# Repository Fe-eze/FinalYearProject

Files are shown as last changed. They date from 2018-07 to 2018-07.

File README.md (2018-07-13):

# FinalYearProject
My final year project. Formula Student: Design of a Battery and Battery Management System

I started by designing the battery from a 20700 (as you see in design 1 & 2 in the deliverables) but had to do a hard pivot when I noticed the design didn't seem to be feasible. The final design was done with 18650 cells.

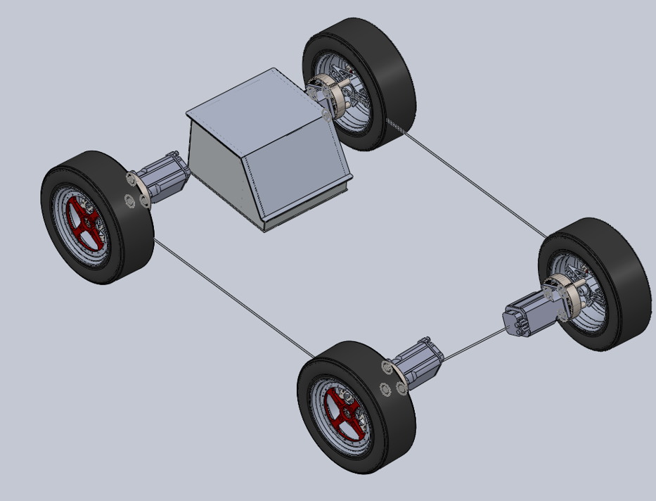
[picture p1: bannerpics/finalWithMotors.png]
Battery Pack with Motors

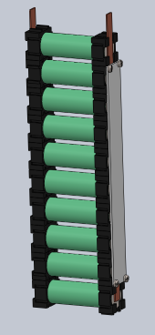
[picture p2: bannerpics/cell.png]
Cells Joined in a string

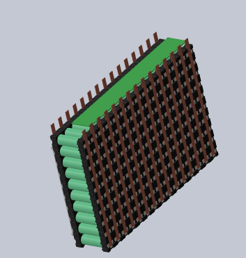
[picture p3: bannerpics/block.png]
Battery Strings joined to form a block

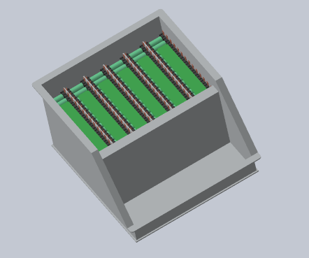
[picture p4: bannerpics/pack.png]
Final Battery Pack

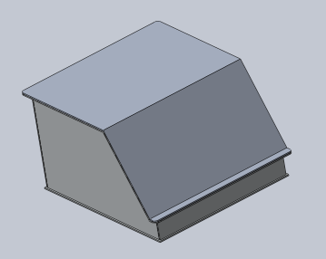
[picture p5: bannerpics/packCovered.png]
Battery Pack with Cover


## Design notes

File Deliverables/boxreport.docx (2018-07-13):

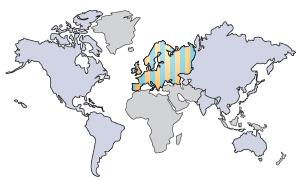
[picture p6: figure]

| Manufacturing Region The choice of manufacturing region determines the energy sources and technologies used in the modeled material creation and manufacturing steps of the product’s life cycle.
| Use Region The use region is used to determine the energy sources consumed during the product’s use phase (if applicable) and the destination for the product at its end-of-life. Together with the manufacturing region, the use region is also used to estimate the environmental impacts associated with transporting the product from its manufacturing location to its use location.

Summary

Learn more about Life Cycle Assessment (http://www.solidworks.com/sustainabilityinfo)

Sustainability Report
Model Name: | | | | | | | | Weight: | | 15856.92 g
| | | | | | | | Built to last: | | 0.417 year
| | | | | | | | Duration of use: | | 5.0 year
Assembly Process Region: Europe Energy type: Electricity Energy amount: 0.00 kWh Built to last: 0.417 year | | | | | | Use Region: Europe Energy type: None Energy amount: 0.00 kWh Duration of use: 5.0 year
Transportation Truck distance: 1900 km Train distance: 0.00 km Ship distance: 0.00 km Airplane Distance: 0.00 km | | | | | | End of Life Recycled: 25 % Incinerated: 24 % Landfill: 51 %

Comments
Click here for alternative units such as ‘Miles Driven in a Car’ (http://www.solidworks.com/plugins/sustainability/calculator.htm?LANG=en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)

Sustainability Report
Model Name: | | | | | | | Weight: | | 15856.92 g
| | | | | | | Built to last: | | 0.417 year
| | | | | | | Duration of use: | | 5.0 year

Environmental Impact (calculated using TRACI impact assessment methodology)
Carbon Footprint Material: 990 kg CO2e Manufacturing: 45 kg CO2e Use: 0.00 kg CO2e Transportation: 23 kg CO2e End of Life: 130 kg CO2e 1200 kg CO2e | | | | | | Total Energy Consumed Material: 1.2E+4 MJ Manufacturing: 750 MJ Use: 0.00 MJ Transportation: 350 MJ End of Life: 95 MJ 1.3E+4 MJ
Air Acidification Material: 320 mol H⁺ e Manufacturing: 15 mol H⁺ e Use: 0.00 mol H⁺ e Transportation: 9.4 mol H⁺ e End of Life: 5.1 mol H⁺ e 350 mol H⁺ e | | | | | | Water Eutrophication Material: 0.086 kg N e Manufacturing: 5.4E-3 kg N e Use: 0.00 kg N e Transportation: 9.0E-3 kg N e End of Life: 0.033 kg N e 0.133 kg N e

Material Financial Impact | 176.10 USD

Comments
Click here for alternative units such as ‘Miles Driven in a Car’ (http://www.solidworks.com/plugins/sustainability/calculator.htm?LANG=en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)

Sustainability Report
Model Name: | | | | | Weight: | 15856.92 g
| | | | | Built to last: | 0.417 year
| | | | | Duration of use: | 5.0 year

Component Environmental Impact

Top Ten Components Contributing Most to the Four Areas of Environmental Impact

Component | Carbon | | | | | | | | | | Water | | | | | | | | | | Air | | | | | | | | | Energy
box_TopCover | 37 | | | | | | | | | | 3.3E-3 | | | | | | | | | | 11 | | | | | | | | | 460
box_base | 33 | | | | | | | | | | 2.9E-3 | | | | | | | | | | 10 | | | | | | | | | 400
box_back | 20 | | | | | | | | | | 1.8E-3 | | | | | | | | | | 6.3 | | | | | | | | | 250
box_side | 20 | | | | | | | | | | 1.8E-3 | | | | | | | | | | 6.2 | | | | | | | | | | 250
box_sidemirrored | 20 | | | | | | | | | | 1.7E-3 | | | | | | | | | | 6.1 | | | | | | | | | 240
box_frontdivider | 17 | | | | | | | | | | 1.5E-3 | | | | | | | | | | 5.4 | | | | | | | | | 220
box_inner | 12 | | | | | | | | | | 1.1E-3 | | | | | | | | | | 3.9 | | | | | | | | | 150
box_front | 5.7 | | | | | | | | | | 5.0E-4 | | | | | | | | | | 1.8 | | | | | | | | | 71

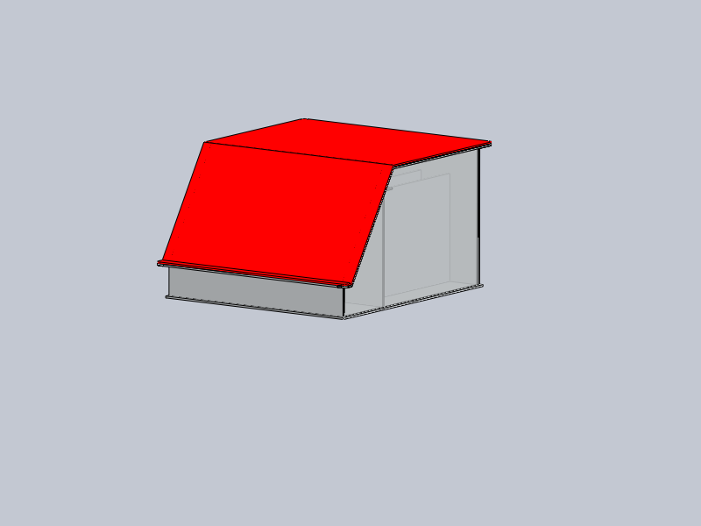
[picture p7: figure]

Comments
Click here for alternative units such as ‘Miles Driven in a Car’ (http://www.solidworks.com/plugins/sustainability/calculator.htm?LANG=en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)

Sustainability Report

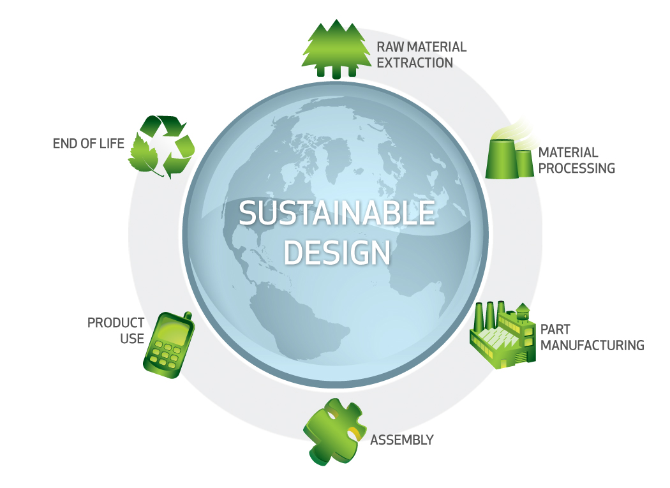
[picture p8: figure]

Sustainability Report

Glossary

Air Acidification - Sulfur dioxide, nitrous oxides other acidic emissions to air cause an increase in the acidity of rainwater, which in turn acidifies lakes and soil. These acids can make the land and water toxic for plants and aquatic life. Acid rain can also slowly dissolve manmade building materials such as concrete. This impact is typically measured in units of either kg sulfur dioxide equivalent (SO2), or moles H+ equivalent.

Carbon Footprint - Carbon-dioxide and other gasses which result from the burning of fossil fuels accumulate in the atmosphere which in turn increases the earth’s average temperature. Carbon footprint acts as a proxy for the larger impact factor referred to as Global Warming Potential (GWP). Global warming is blamed for problems like loss of glaciers, extinction of species, and more extreme weather, among others.

Total Energy Consumed - A measure of the non-renewable energy sources associated with the part’s lifecycle in units of megajoules (MJ). This impact includes not only the electricity or fuels used during the product’s lifecycle, but also the upstream energy required to obtain and process these fuels, and the embodied energy of materials which would be released if burned. PED is expressed as the net calorific value of energy demand from non-renewable resources (e.g. petroleum, natural gas, etc.). Efficiencies in energy conversion (e.g. power, heat, steam, etc.) are taken into account.

Water Eutrophication - When an over abundance of nutrients are added to a water ecosystem, eutrophication occurs. Nitrogen and phosphorous from waste water and agricultural fertilizers causes an overabundance of algae to bloom, which then depletes the water of oxygen and results in the death of both plant and animal life. This impact is typically measured in either kg phosphate equivalent (PO4) or kg nitrogen (N) equivalent.

Life Cycle Assessment (LCA) - This is a method to quantitatively assess the environmental impact of a product throughout its entire lifecycle, from the procurement of the raw materials, through the production, distribution, use, disposal and recycling of that product.

Material Financial Impact - This is the financial impact associated with the material only. The mass of the model is multiplied by the financial impact unit (units of currency/units of mass) to calculate the financial impact (in units of currency).

Learn more about Life Cycle Assessment (http://www.solidworks.com/sustainabilityinfo)

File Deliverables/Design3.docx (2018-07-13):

Design III – Final Design

1. Mechanical Configuration

Battery Module

The battery module is assembled by taking six Sanyo 20700A cells, Adding an M12 Plastic Spacer and then finally the Cu101 conductor. A fuse wire (see electrical section) is welded in the hole between the battery and conductor. This wire acts as the last line of defence in the case of an overcurrent during charging or the first line in the case of a battery Short Circuit. Six of these cells are connected in parallel and they collectively make one battery module. There are 90 such modules in the entire battery pack (Making a total of 540 cells).

Integrated Module Busbar

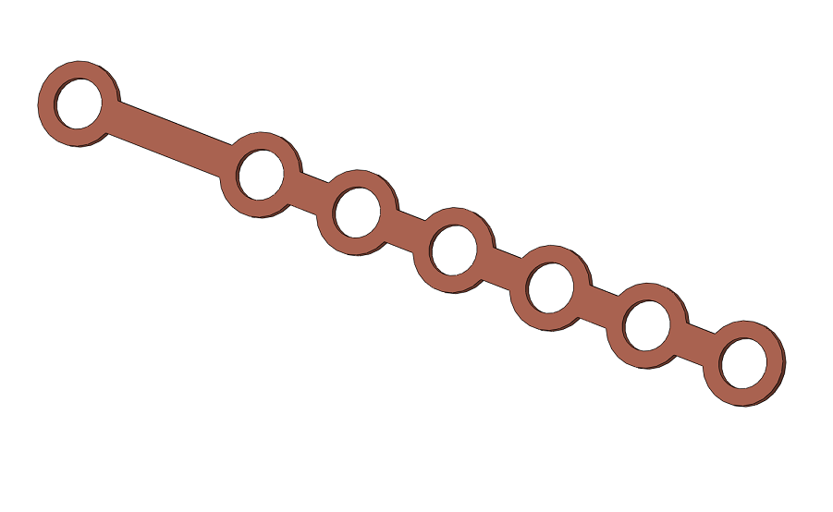
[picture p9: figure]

The Module Busbar will be made of Cu101 grade Copper. It will run along the side of the cells (both +ve and -ve) and connect to them via fusible link wires. The top cylinder will be bent and inserted into the module cap where it will be connected in series with other modules and bolted down with an M10 Nut

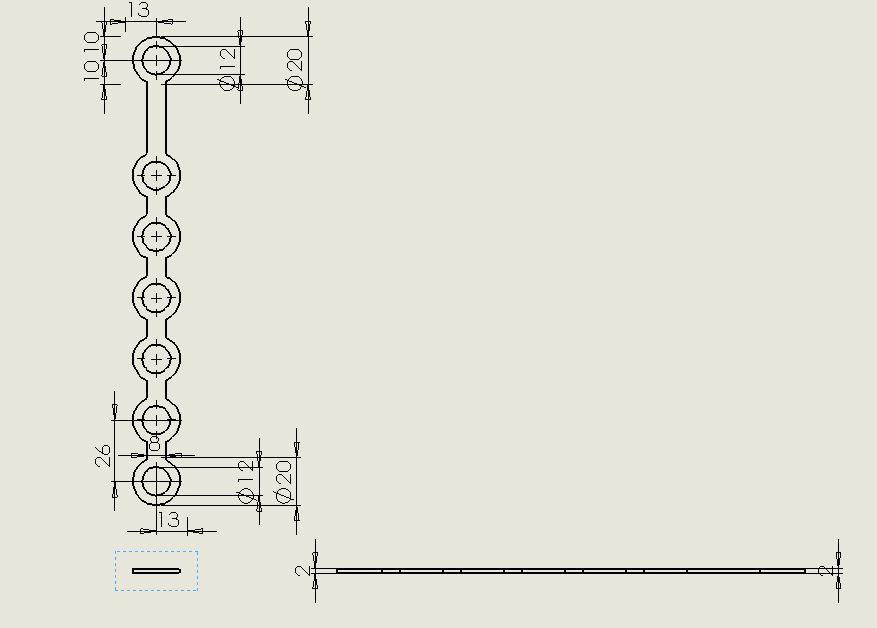
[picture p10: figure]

Module Cap

The Module Cap will be made of ABS Plastic. It has two circular holes at the top where an M10 bolt will be fastened to join the modules in series. There is a side cut to allow insertion of an M10 nut and finally, the rectangular holes at the sides will let the Conductor through from the Module Side Insert

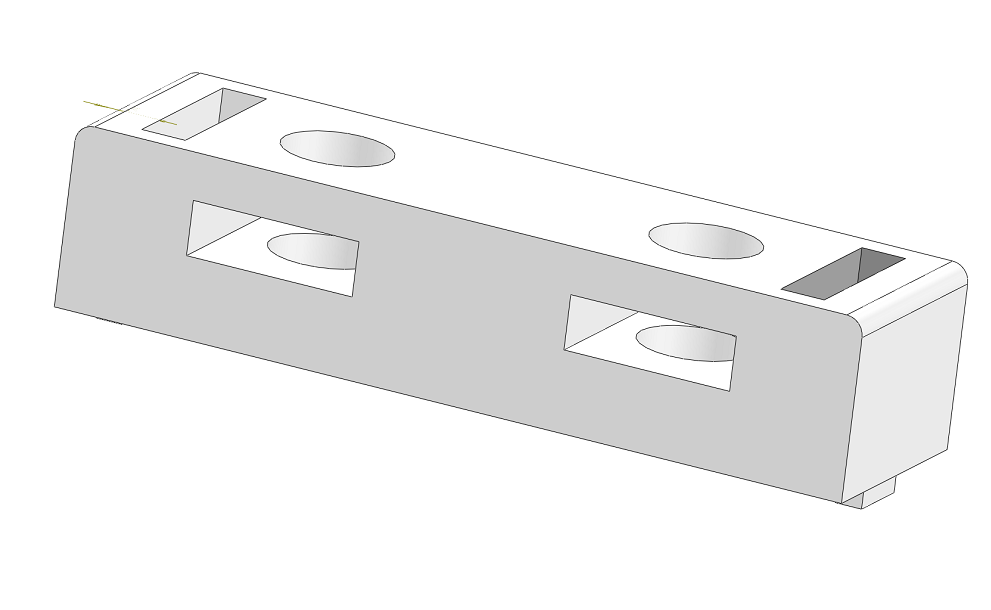
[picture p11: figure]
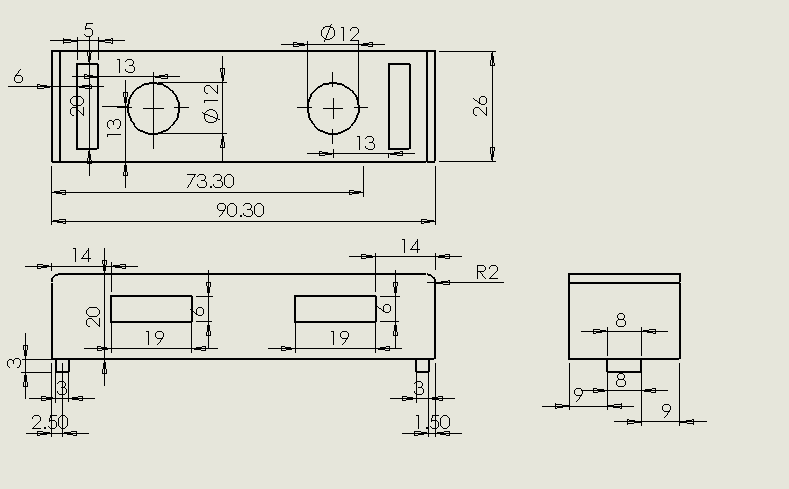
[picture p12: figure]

Module Side Insert

The Module Side insert (made with ABS) will accommodate the copper busbars. The circular spaces are 1mm larger than the busbar diameter to ensure a nice fit. ABS has a high tolerance of up to 110C so is adequate for our battery housing purposes.

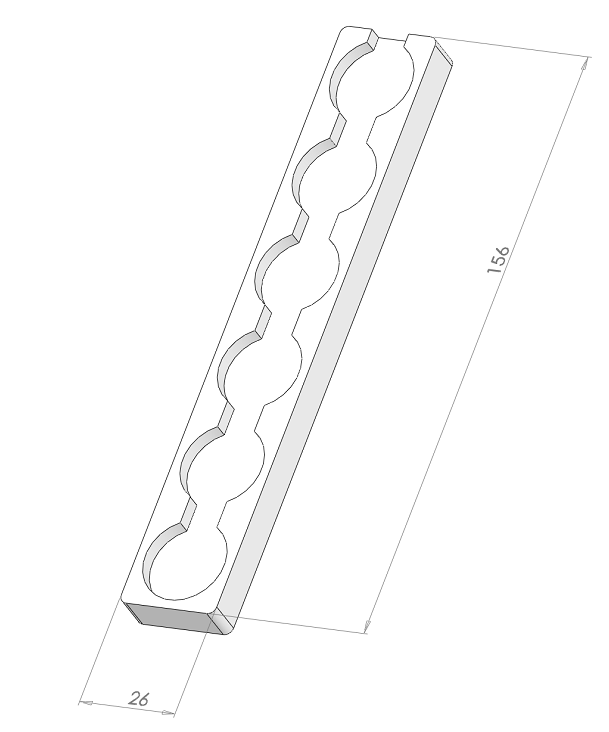
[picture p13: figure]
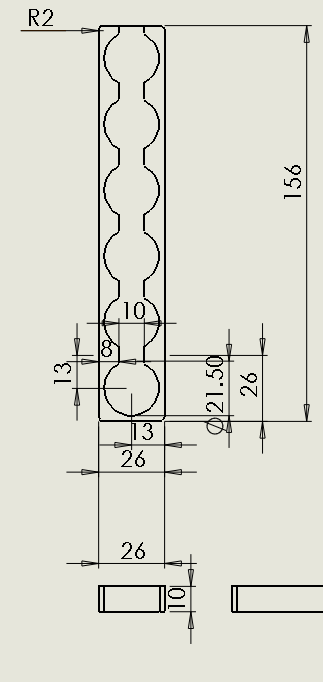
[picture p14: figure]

Assembling Battery Module

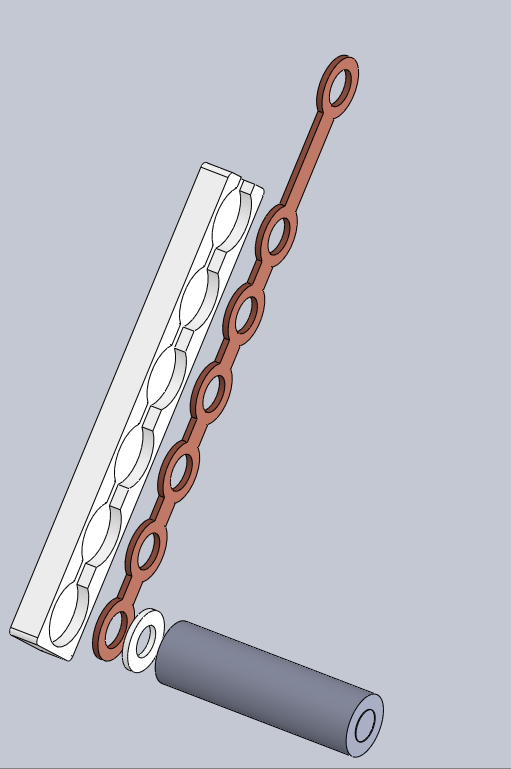
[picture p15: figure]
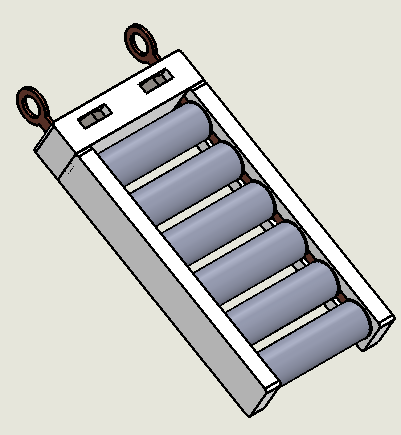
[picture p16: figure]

Left: Visualizing Module Assembly Steps

Right: Final Module Assembly (Note the M10 Nut inserted into the Module cap)

Each module is in effect an 18.6A (3.1A*6), 3.6Volt battery and 90 modules (18 per section *5sections) will be connected in series to give us a final pack voltage of 324V, I=18.6A (at 1C Discharge, 180A Max. Continuous discharge), P=6.026kW/4.338MJ.

Section Calculations

EV3.3.3 states that each section must be no greater than 120V, 6MJ.

Our section design here is 3.6V*18=64.8V /1.205kWh/ 4.336MJ which meets the requirements.

Battery box assembly

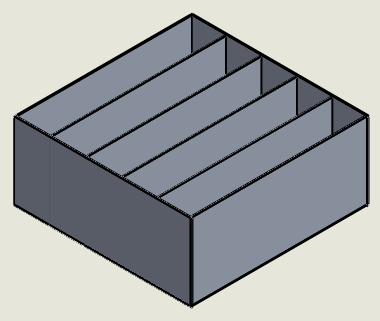
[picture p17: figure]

The battery box will be made of a 3.2mm thick, 464.2mm*468mm 6061-TS Aluminium plate as a base with four 2.3mm walls (and 200mm high) fastened with M8 bolts to divide the box into five sections and finally four 2.3mm thick external walls (205mm high) fastened with M8 bolts. The internal walls will then be covered with fire retardant formex and 18 modules inserted in each section. The PCB for each section will be inserted in the 32mm gap between the top of the modules and the top of the internal vertical wall.

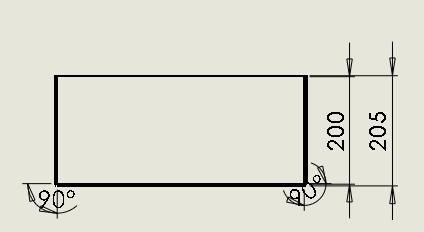
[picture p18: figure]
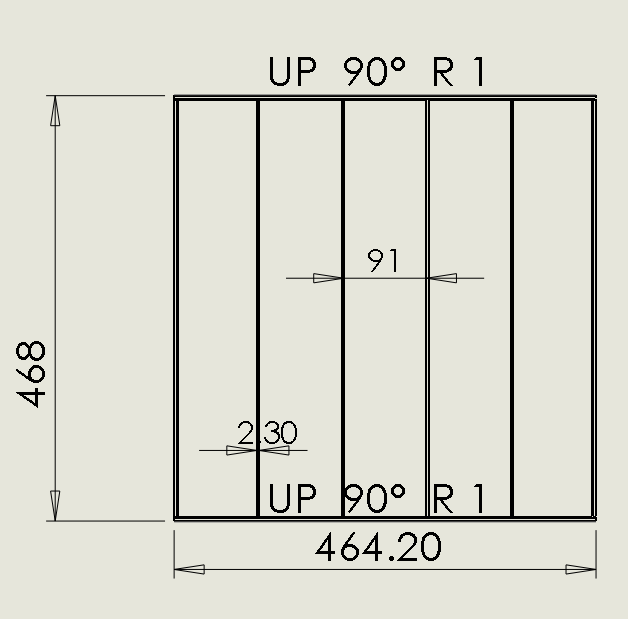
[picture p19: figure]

2. Electrical Configuration

Battery Management System

Temperature Acquisition Circuit

The temperature sensors will be placed at the end of each cell. The sensor selected is a Texas Instruments LMT-84 in a TO-92 Package. This will be inserted into the module PCB which then connects to a module multiplexer. This multiplexer selects one cell per module and sends the temperature value to the Analog to Digital Converter (ADC), once the temperature is converted and sent to the microcontroller, the microcontroller signals to the multiplexer to take the next cell temperature and this goes on until all six cells in a module are measured. Since there are 18 modules in each section, there will be three such ADCs per section. Each ADC is responsible for six modules. (see block diagrams below) The ADCs send the digital information of the cell temperatures to the Microcontroller using I²C communication. Instead of directly reading all 108 cells in a section (6 cells * 18 modules) which will require 108 analog pins or 18pcs of 8-channel ADCs, we are able to save space and cost by using a local multiplexer to switch temperatures.

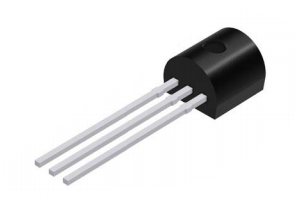
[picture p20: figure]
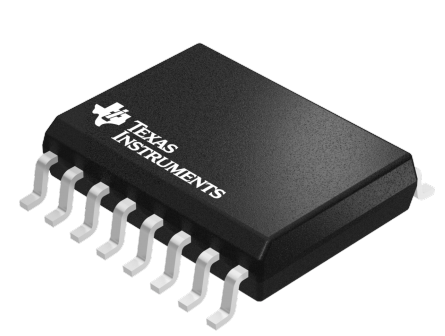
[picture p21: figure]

LMT84 Temperature Sensor and SN74LVxx MUX

The LMT84 is a precision CMOS temperature sensor which has a linear Voltage to temperature behaviour making it superior to NTC sensors (which have nonlinear behaviour and are very much affected by self-heating). It operates between 1.5V to 5V (VDD)

The TI SN74LV4051A-Q1 is an Automotive rated 8 Channel CMOS multiplexer that has one output. The switching is done by the microcontroller and all 90 modules will have their local MUX unit which will all be connected by the same four GPIO pins from the µC. It comes in a compact 8.89*10.63*2.65mm SOIC package and will be inserted in a PCB just above the modules in the battery box. 2V < VDD <5.5V

The TI ADS7828-Q1 is an Automotive rated 12-bit, 8 Channel Analog to Digital Converter (ADC) with an I2C communications port and a 50kHz Sampling rate. It comes in a TSSOP 6.4*5mm package. 2.7V < VDD <5V

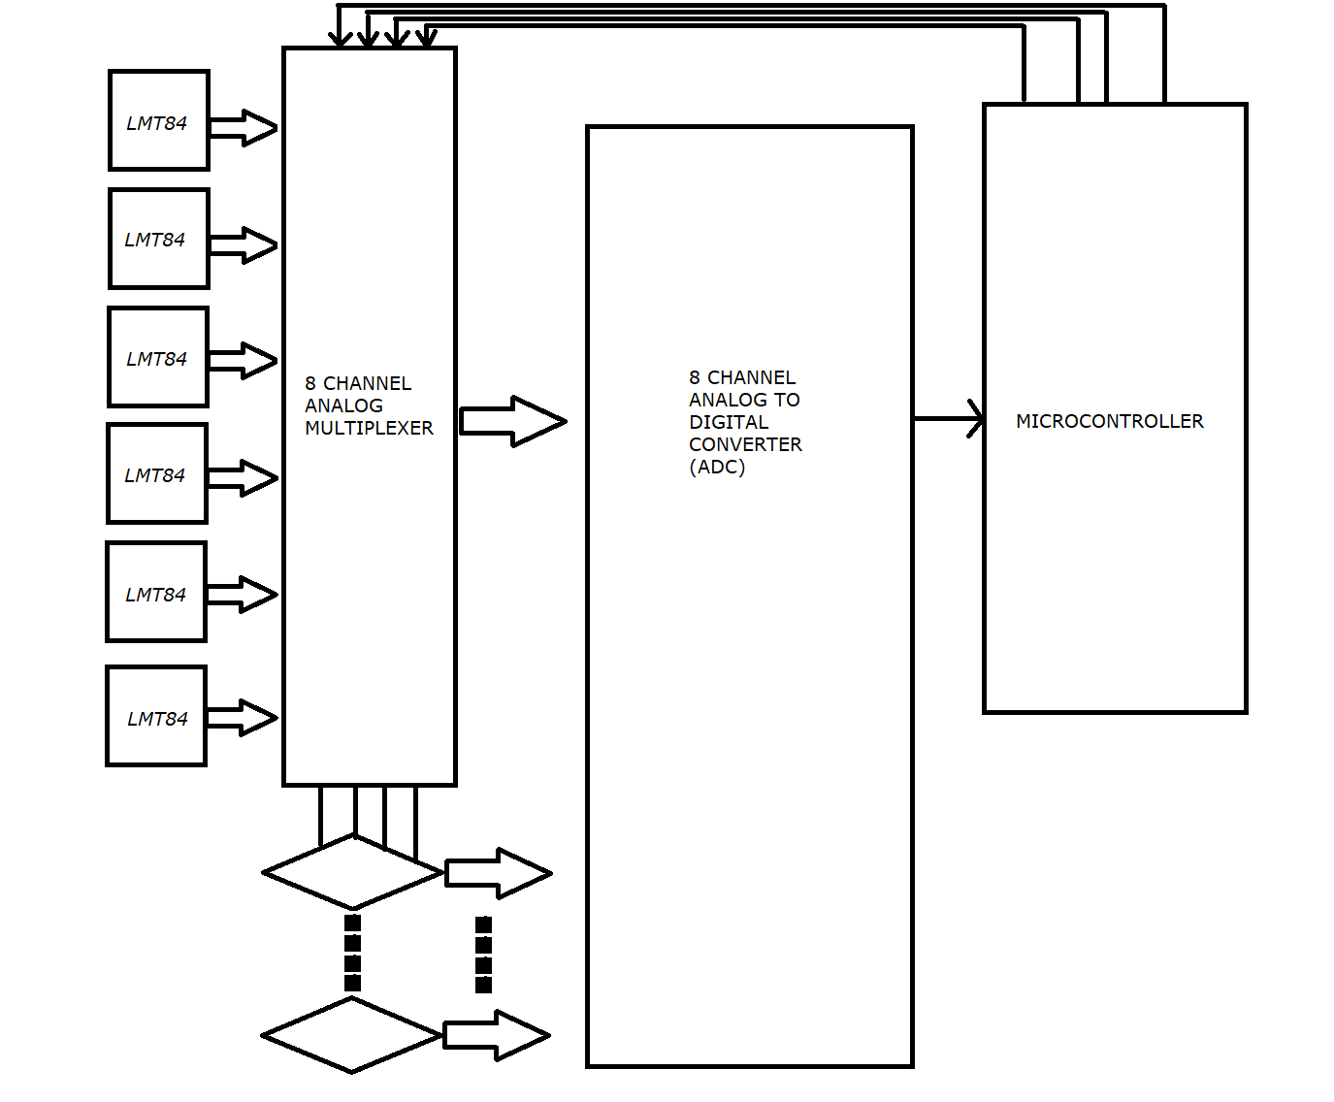
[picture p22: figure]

Temperature Acquisition Block Diagram (Thick arrows indicate Analog Paths; thin arrows indicate Digital Paths)

Battery Protection

A Renesas ISL92403 IC will be used for battery monitoring, protection and voltage balancing. It has a capacity of 3-8 cells but since our modules are in parallel, each monitor IC will handle 6 modules (i.e. 36 cells) and there will be three per section. It is a semi-autonomous unit that can do all the protection tasks required without the help of a microcontroller(µC), it has I²C communications capability and this will be used by the µC sparingly. This design ensures the micromanagement is done locally and the µC will be for data logging, coulomb counting and last resort interference.

Fuse Wire Rating

We want our fuse wire to melt when current goes over 30A in five seconds

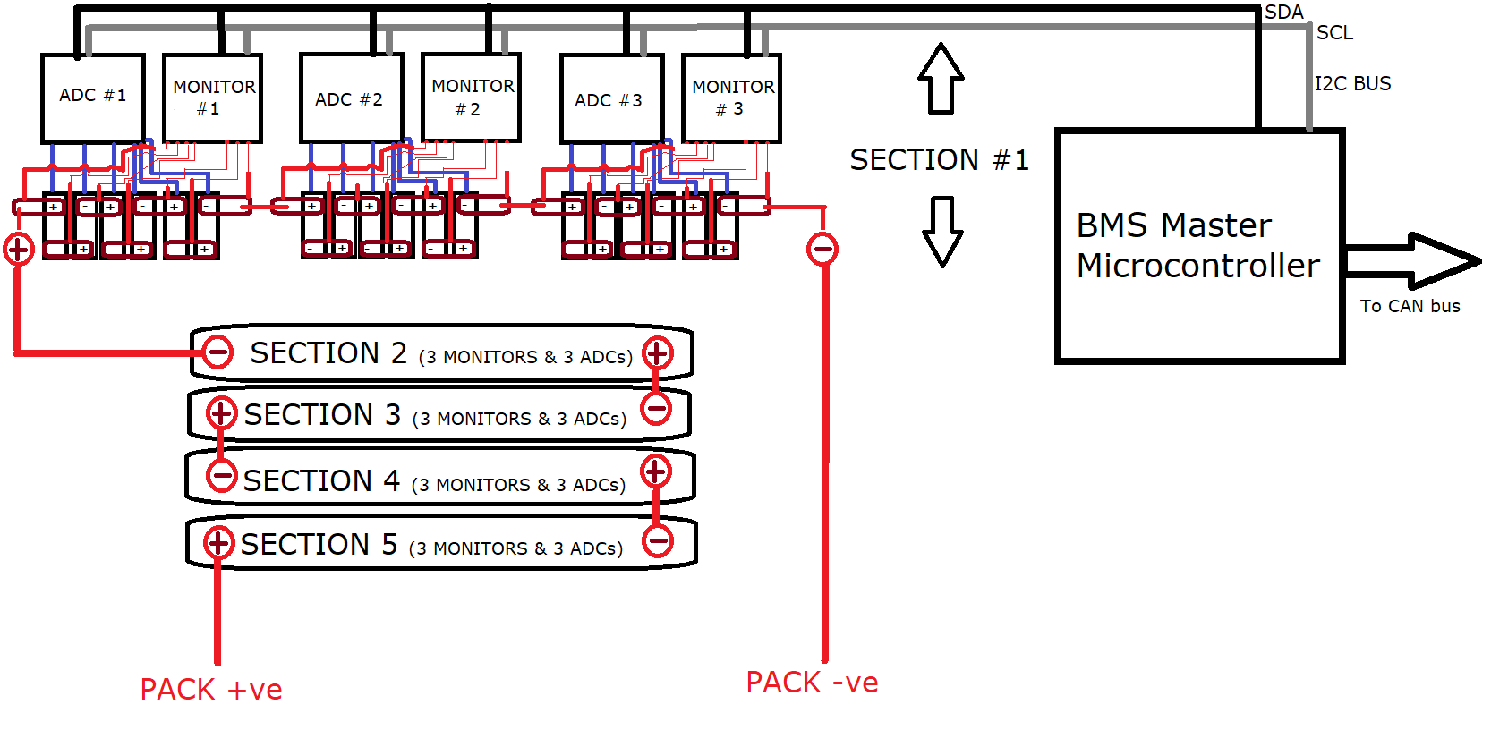
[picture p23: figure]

BMS block diagram – Thick red is high voltage, thin red is voltage sense, black and grey are the bidirectional communications channels on the I²C bus (one line for data, and one for the clock), Blue is the Temperature sense (explained above)

Manufacture Plan

3D printing can be used for the rapid prototyping and testing stage. However, because of the cost of 3D printing 90*2=180 side inserts, it is more economical to use injection moulding when the full pack is ready to be produced. The cost of the moulding tool and the will be cheaper than 3D printing all the Plastic parts and if we want to make a standby battery box (to implement the proposed fast change battery feature), the presence of the moulding tool makes it astronomically cheaper the second time around (this shall be explored further in the Cost Report)

The copper busbars will be CNC milled from 2mm thick rectangular Copper bars

Each module will require one PCB running along the side of the ABS side part (to acquire the temperature) and Each section will require one PCB running along the top where the six slave I2C Devices (ADCs and Monitors) will be mounted.

Future work

Testing of design

The circuit will have to be fully simulated and corrections made before the parts are purchased

Stress Testing of Battery Box

The battery box would have to be further analysed using FEA to make sure it can withstand stresses required (40g longitudinal and lateral Acceleration, and 20g vertical acceleration)

Full thermal characteristics to devise cooling system

The cooling systems cannot be devised just yet because the thermal characteristics of the cell are currently unknown. In the new year, a specimen of the cell will be acquired, and an equivalent circuit based on the cell’s thermal behaviour will be made. Then, it will be simulated over racing conditions and the temperature behaviour observed. It is at this point that a cooling system will be picked.

BMS software will have to be written to convert all internal I²C communications to CAN format so that the BMS can interact with the main vehicle ECU over a CAN bus.

[Type text][Type text][Type text]

Formula StudentCITY RACING 20188

Formula StudentCITY RACING 20181

Name: Fe-eze Anyafulu Programme & Part: Electrical Engineering Part 4 Project Role: EV Battery System Subgroup: Electric Vehicle Frontline Task: EV Team Lead

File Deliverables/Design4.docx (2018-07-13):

Design V- Cost and Sustainability Report

Bill of Materials

The following pages contain the bought parts and made parts (with detailed processes) that go into making the High Voltage battery and Battery Management System

Some notes for Mass manufacture

- While it may be viable to assemble the Printed circuit boards by hand for the prototypes, it becomes cost prohibitive and excessively time consuming in the case of mass manufacture hence it would be better to outsource this process to a contract manufacturer.
- It would be better to used bent sheet metal for the battery box as opposed to riveted parts when it comes to mass manufacturing.

Sustainability Report

Sustainability report was carried out on the battery box and the assembled battery sections which will go into the box (the bricks). The box was set to be manufactured and used in Europe while the battery section was set to be manufactured in Asia and used in Europe. The results are shown below:

Map

| Manufacturing Region The choice of manufacturing region determines the energy sources and technologies used in the modeled material creation and manufacturing steps of the product’s life cycle.
| Use Region The use region is used to determine the energy sources consumed during the product’s use phase (if applicable) and the destination for the product at its end-of-life. Together with the manufacturing region, the use region is also used to estimate the environmental impacts associated with transporting the product from its manufacturing location to its use location.

Environmental Impact (calculated using TRACI impact assessment methodology)
Carbon Footprint Material: 990 kg CO2e Manufacturing: 45 kg CO2e Use: 0.00 kg CO2e Transportation: 23 kg CO2e End of Life: 130 kg CO2e 1200 kg CO2e | Total Energy Consumed Material: 1.2E+4 MJ Manufacturing: 750 MJ Use: 0.00 MJ Transportation: 350 MJ End of Life: 95 MJ 1.3E+4 MJ
Air Acidification Material: 320 mol H⁺ e Manufacturing: 15 mol H⁺ e Use: 0.00 mol H⁺ e Transportation: 9.4 mol H⁺ e End of Life: 5.1 mol H⁺ e 350 mol H⁺ e | Water Eutrophication Material: 0.086 kg N e Manufacturing: 5.4E-3 kg N e Use: 0.00 kg N e Transportation: 9.0E-3 kg N e End of Life: 0.033 kg N e 0.133 kg N e

Material Financial Impact | 176.10 USD

Comments

Component Environmental Impact

Top Ten Components Contributing Most to the Four Areas of Environmental Impact

Component | Carbon | | | | | | | | | | Water | | | | | | | | | | Air | | | | | | | | | Energy
box_TopCover | 37 | | | | | | | | | | 3.3E-3 | | | | | | | | | | 11 | | | | | | | | | 460
box_base | 33 | | | | | | | | | | 2.9E-3 | | | | | | | | | | 10 | | | | | | | | | 400
box_back | 20 | | | | | | | | | | 1.8E-3 | | | | | | | | | | 6.3 | | | | | | | | | 250
box_side | 20 | | | | | | | | | | 1.8E-3 | | | | | | | | | | 6.2 | | | | | | | | | | 250
box_sidemirrored | 20 | | | | | | | | | | 1.7E-3 | | | | | | | | | | 6.1 | | | | | | | | | 240
box_frontdivider | 17 | | | | | | | | | | 1.5E-3 | | | | | | | | | | 5.4 | | | | | | | | | 220
box_inner | 12 | | | | | | | | | | 1.1E-3 | | | | | | | | | | 3.9 | | | | | | | | | 150
box_front | 5.7 | | | | | | | | | | 5.0E-4 | | | | | | | | | | 1.8 | | | | | | | | | 71

[Type text][Type text][Type text]

Formula StudentCITY RACING 20183

Formula StudentCITY RACING 20181

Name: Fe-eze Anyafulu Programme & Part: Electrical Engineering Part 4 Project Role: Electric Vehicle Battery System Subgroup: Electric Vehicle Frontline Task: EV Team Lead

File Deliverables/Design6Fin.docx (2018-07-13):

Electric Vehicle Subgroup

Final Report

Ahmed Abid-Ali

Fe-eze Anyafulu

MEng Electrical Engineering Part 4

City, University of London

11 June 2018

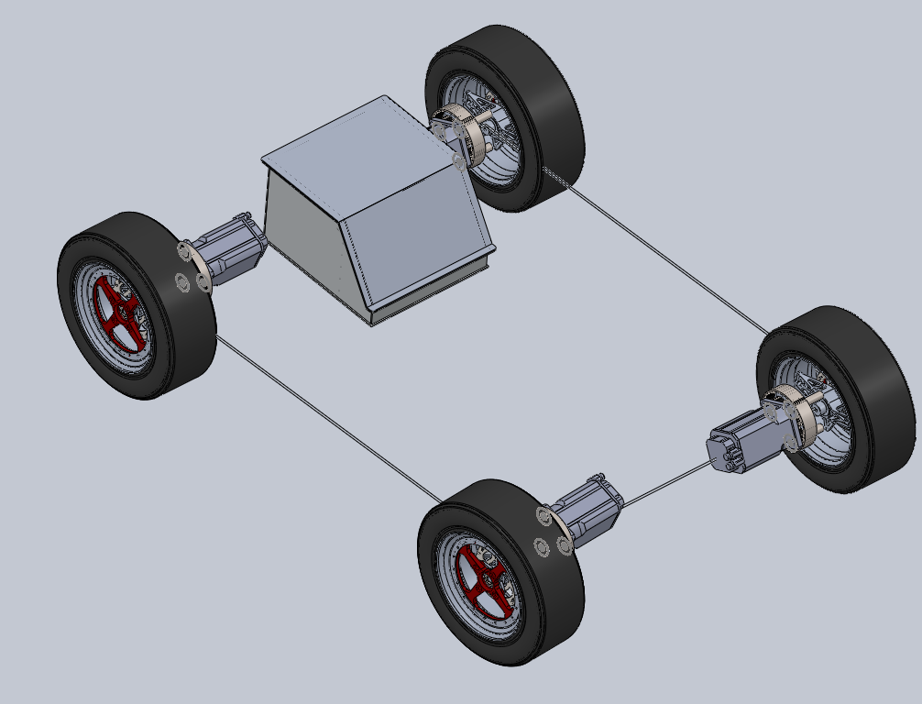
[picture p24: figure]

# 1 Introduction

Electric vehicles can achieve greater energy efficiency than internal combustion vehicles (90% vs ~30%) because the energy is supplied straight to the wheels with minimal losses whereas an IC engine loses a lot of energy to heat. better for environment

Electric vehicles are also able to achieve faster acceleration compared to their gasoline counterparts. It is for these reasons that we set out to design and build the core of an electric vehicle. While it was initially our goal to design the entire vehicle, the scope was reduced to focus on the core of the EV (the energy supply and drivetrain).

# 2 Drivetrain

# 2.1 Introduction

Electric motors are responsible in converting the electrical energy stored in the battery into mechanical energy, which in turn, propels the car at the required speed. Since the Formula student competition consists of the static and dynamic event, one needs to ensure that the design of the drivetrain can provide the right performance for each event; The drivetrain consists of the electric motor. Therefore, the choice and design of the drivetrain will depend on different factors such as: weight, torque, speed, power to weight ratio, which will be analysed when deciding what drivetrain configuration to use.

# 2.2 Aims and objectives

The aims and objectives in designing the drivetrain involves a high-performance system, low weight, and at the same time meet the regulations set. For the drivetrain, the total maximum power drawn by the electric motors from the battery cannot exceed 80 kW.

## 2.2.1 Performance

A high pace must be achieved by the driver, or in other words a high performance must be delivered by the system to ensure the driver can accelerate fast. An electric motor must therefore be able to provide high enough torque in those situations.

# 2.3 Different conceptual designs

Since the rules specify and limit the power drawn from the battery to be 80 kW, the next step is to analyse different drivetrain configurations which will provide the best performance in terms of acceleration and agility as well as high power to weight ratio. There are many different configuration systems that can be applied such as: front wheel drive, rear wheel drive or four-wheel drive. They all serve the same purpose of propelling the car. However, the type of configuration chosen will have a different effect on the acceleration, agility as well as the total weight of the car. By utilising the front wheel drive configuration or the rear wheel drive system, there are only 2 wheels being engaged in driving the car, whereas, the other two wheels are not contributing. On the other hand, the four-wheel drive system ensures that all wheels are contributing in driving the car and this has shown to provide higher acceleration even though more power is consumed [1].

The preferred weight distribution when designing the electric vehicle is 50:50 (front: rear). This is to distribute the power required for each motor more evenly and hence the efficiency will increase [2].

## 2.3.1 Analysing the forces acting on a four-wheel drive system

To calculate the forces that are exerted on the vehicle by a 4 in wheel drive system, figure 1 was used to calculate the minimum requirements when choosing a motor.

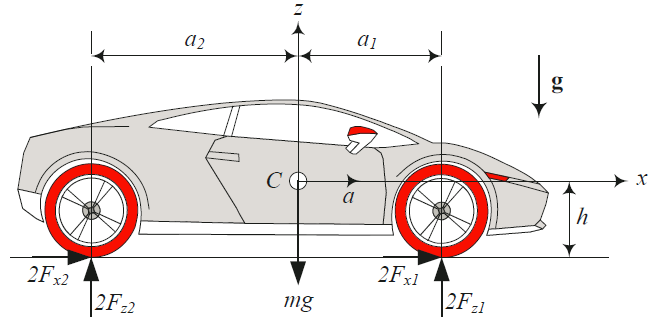
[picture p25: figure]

Figure 1: Shows the forces that are exerted on the car for a 4 in wheel motor configuration system

Using equations of motion for the accelerating car, Newton’s equation, in x-direction and two static equilibrium equations in y and z-direction.

∑ F_x =ma (1.1) ∑ F_z =0 (1.2)

∑ M_y =0 (1.3)

Expanding the equations produces three equations for four unknowns F_(x1) , F_(x2) , F_(z1) , F_(z2) .

2F_(x1) +2F_(x2) =ma (1.4)

2F_(z1) +2F_(z2) -mg=0 (1.5)

-2F_(z1) b_1 +2F_(z2) b_2 -2(F_(x1) +F_(x2) )h=0 (1.6)

To solve for the normal forces F_(z1) and F_(z2) , we would need to eliminate ( F_(x1) +F_(x2) ) between the equations 1.4 to 1.6.

F_(z1) =(F_(z1) )_(st) +(F_(z1) )_(dyn) =1/2mg(b_2)/l-1/2mah/l (1.7)

F_(z2) =(F_(z2) )_(st) +(F_(z2) )_(dyn) =1/2mg(b_1)/l+1/2mah/l (1.8)

The static parts of equation (1.7) and (1.8) are weight distribution for a stationary car and depend on the horizontal position of the mass centre. However, the dynamic parts indicate the weight distribution because of horizontal acceleration and depend on the vertical position of the mass centre.

## 2.3.2 Maximum acceleration on a level road

The maximum acceleration of a car is proportional to the friction under its tires. We assume the friction coefficients at the front and rear tires are equal and all tires reach their maximum traction at the same time.

Fx_1 =-+µ_x F_(z1) Fx_2 =-+µ_x F_(z2) (1.9)

Newton’s equation (1.4) can now be written as

ma=-+2µ_x (F_(z1) +F_(z2) ) (1.10)

Substituting F_(z1) and F_(z2) from (1.7) and (1.8) results in

a=-+µ_x g (1.11)

## 2.3.3 Requested torque

To evaluate the longitudinal dynamic behaviour of the vehicle, the movement resistance forces such as the rolling resistance ( R_x ), estimated by (2.1), and the aerodynamic drag, estimated by (2.2), need to be considered when calculating the torque required [2].

The rolling resistance ( R_x ) is related to the energy lost by the tire deformation and adhesion on contact area. It is the function of the vehicle weight (W) (N), multiplied by a dimensionless rolling resistance coefficient that expresses the effects of the interdependent physical properties of tire and ground as a function of the vehicle speed (V) (m/s)

R_x =W(0.01+2.24*10^(-4) V) (2.1)

The air resistance against the car passage is named the aerodynamic drag ( D_A ). This resistance force is defined by the air density (ρ) (kg/ m^3 ), the vehicle frontal area (A) ( m^2 ) and an empirical constant based on the vehicle geometry known as drag coefficient ( C_D ) as shown in the following equation:

D_A =1/2ρV^2 C_D A (2.2)

The requested torque ( T_(req) ) is shown by (2.3) as a function of the vehicle acceleration ( a_x ) ( m/s^2 ), mass (M) (kg), the tire external radius (r) (m) and the wheels and tires inertia ( I_W ) ( kgm^2 ) in which are also considered the in-wheel motors inertia

T_(req) =(Ma_x +(I_W a_x)/(r^2)+R_x +D_A )r (2.3)

# 2.4 Motor requirement calculations

Assumptions

- Mass with driver (M): 280 [kg]
- Wheelbase: 1.525 [m]
- Tyre rolling radius (r): 5” ≜ 0.127 [m]
- Coefficient of friction (μ): 1.2
- CoG height (h): 0.2 [m]
- Weight Distribution: 50:50
- Maximum power: 80 [kW]
- Inertia of tires and wheels ( I_w ): 1*10^(-3) [kg m^2 ]
- Frontal area (A): 0.77 [ m^2 ]
- Drag coefficient ( C_D ): 0.69
- Air density ( ρ ): 1.225 [kg/ m^3 ]

Using Equation (1.11) to work out the maximum acceleration.

a=1.2*9.81≜11.772 [m/s^2 ]

The torque through the rear wheel can be calculated by using (1.8).

Rear Torque (T_r )=Frictional Force (F_(z2) *µ)*rolling wheel radius

T_r =[(1/2*280*9.81*0.7625/1.525)+(1/2*280*11.772*0.2/1.525)]*1.2*0.127

T_r =137.59 [Nm]

The torque through the front wheel can be calculated by using (1.7).

Front Torque (T_f )=Frictional Force (F_(z2) *µ)*rolling wheel radius

T_f =[(1/2*280*9.81*0.7625/1.525)-(1/2*280*11.772*0.2/1.525)]*1.2*0.127

T_f =71.71 [Nm]

Total torque would then be:

Total torque=2T_r +2T_f

Total torque=2*137.59+2*71.71≜418.61232 [Nm]

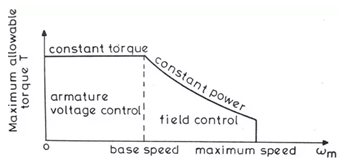
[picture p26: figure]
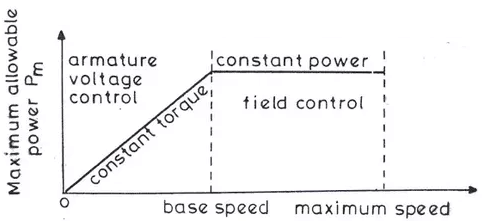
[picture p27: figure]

(a) (b)

Figure 2: Shows the electric motor torque-speed curve. (a) Torque [Nm] against angular velocity [rad/s]. (b) Power [W] against angular velocity [rad/s]

To calculate the speed when maximum power is achieved, the following equation for power was be used:

Maximum Power(P_m )=Requested torque (T_(req) )*Angular Velocity(w)

w=(P_m)/(T_(req))≜(P_m)/((Ma_x +(I_W a_x)/(r^2)+R_x +D_A )r) (3.1)

Since we know that the angular speed is related to the velocity and the tyre rolling radius, Equation (3.1) can be written as:

v/r=(P_m)/((Ma_x +(I_W a_x)/(r^2)+R_x +D_A )r) (3.2)

The above equation can then be further simplified as:

v/r[Ma_x +(I_W a_x)/(r^2)+[W(0.01+2.24*10^(-4) V)]+[1/2ρV^2 C_D A]]r=P_m

(1/2ρC_D A)V^3 +(2.24*10^(-4) W)V^2 +(Ma_x +(I_W a_x)/(r^2)+0.01W)V=P_m

Substituting in the known values in the above equation results in:

(0.3254)V^3 +(0.61528)V^2 +(3324.3579)V=80,000

Solving the above cubic expression results in the velocity of:

V=22.8073 [m/s]

## 2.5 Requested torque

Now that the speed for when the maximum power is achieved has been calculated we can finally calculate the requested torque when maximum power is achieved, equations (2.1), (2.2) and (2.3), by using the obtained value (24.27 [m/s]).

R_x =280*9.81(0.01+2.24*10^(-4) *22.8073)≜41.50 [N]

D_A =1/2*1.225*22.8073^2 *0.69*0.77≜161.27 [N]

T_(req) =(280*11.772+(1*10^(-3) *11.772)/(0.127^2)+41.50+161.27)*0.127≜445.474 [Nm]

## 2.6 Calculating maximum speed reached at 75 [m]

To specify the maximum speed required by the motor, the speed when the car accelerates to 75 [m] is calculated. This is done by using Figure 2 and calculating the work done, by calculating area under the graph, to reach 75 [m]. Firstly, the area when the motor has reached the maximum power is calculated, which is from 0 to base speed as shown on figure 2(a). The distance travelled before maximum power is reached:

- Initial speed: 0 m/s
- Final speed when max power reached: 22.8073 m/s
- Acceleration: 11.772 m/s^2

v^2 =u^2 +2as

s=(22.8073^2)/(2*11.772)≜ 22.093[m]

Therefore, work done during constant torque phase:

Work done=Total traction force*distance moved in the direction of the force

Work done=445.474/0.127*22.093=77496.39 [J]

To work out the work done through the constant power phase the following equation was used:

work done=³√((9P^2 x^2)/8)

where x represents the distance travelled (m), P represents the constant power (W). Using above equation:

work done=³√((9*80,000^2 *(75-22.093)^2)/8≜27213.467 [J])

The total work done is therefore:

Total work done=77496.39+27213.467≜104709.86 [J]

The final speed reached when travelling 75m is then calculated by equating the total work done to the kinetic energy gained:

KE=1/2Mv^2 =104709.86

v=√((104709.86 *2)/280)=27.35 [m/s]

Converting it to rpm

rpm=v/r60/(2π)≜2056.35 [rpm]

## 2.7 Motor specification

The motor specification required is shown on Table 1.

Halt to max power | | Rear | Front | Total
| Torque (Nm) | 146.42 | 76.31 | 445.47
| RPM () | 1714.90 | 1714.90
Max power to 75 m | Torque (Nm) | 122.11 | 63.64 | 371.50
| RPM | 2056.35 | 2056.35

Table 1: The minimum motor specification required

## 2.8 Choosing a motor

Now that the calculations regarding the minimum torque as well as motor speed required when deciding on which motor to select has been done, a decision on which motor was made. There are many different types of motors available. However, the type of motor decided to use is a servomotor since they are designed to include an encoder which is used to calculate the speed of the motor. AMK is a company which sells servomotors and provide with a motor that meet our motor specification. More specifically AMK DD5-14-10 was chosen and its specification is illustrated on Table 1 which is a synchronous motor. Water cooling was chosen as the cooling type instead of air cooling since the aerodynamics of the car will not be affected as well as a simpler design. This will be at the cost of adding additional cost as well as weight of the total car.

Motor | Weight [kg] | Torque [Nm] | Power [kW] | Torque/ Weight | Size [ m^3 ] | Diameter [mm] | Moment of inertia [kg cm^2 ] | Speed [rpm]
AMK DD5-14-10 | 3.55 | 21 | 37 | 23.25 | 0.00075 | 24 | 2.74 | 20,000

Table 1: Motor specification of single AMK DD5-14-10 motor

# 2 Transmission system

Since the torque provided by the AMK DD5-14-10 does not meet the minimum requirement, a transmission system will have to be implemented and used. A transmission system allows to alter the output torque in the expense of higher motor speed. There are many transmissions systems which could be used, but due to simplicity and high reliability, an epicyclic gear box was chosen. Due to the manufacturing of the epicyclic gearbox requiring to be very precise, it was decided to be bought. A 3:1 epicyclic gearbox ratio was chosen from HMK which meets the nominal requirements shown below on Table 2.

Halt to max power | | Rear | Front | Total
| Torque (Nm) | 48.81 | 25.44 | 148.49
| RPM () | 5144.71 | 5144.71
Max power to 75 m | Torque (Nm) | 40.70 | 21.21 | 123.83
| RPM | 6169.06 | 6169.06

Table 2: Nominal requirements of the epicyclic gearbox.

# 3 Motor Controller

A drive is required to provide the required current and voltage which will control the torque and speed, respectively. Moreover, there are different types of motor controllers available for different purposes. For the car to be able to regenerate power during braking (regenerative braking), a motor controller which is able to control drives in 4-quadrant operation is therefore a necessity. This will ensure that when the driver wants to accelerate that the EMs behave as motors. On the other hand, when the driver is braking the EMs must behave as generators to transfer the mechanical energy into electrical energy. This has several advantages including: reducing the wear caused by braking pads since less force is required, energy will be restored into the battery which will increase the duration as well as the distance the car is able to travel. The motor controller is provided by AMK which supports 4 quadrant control, it is called the AMK KWS 26.

# 4.1 Front line task

As part of my front-line task, my responsibility was the fundraising of the EV. This means that certain tasks need to be carried out to recruit sponsors to purchase some parts. The completion of the BLC report was a huge part for my front-line task since it required to conduct a market research in the form of a questionnaire. This was done to get a better understanding of what was expected in terms of: the price that the customers were willing to pay, the target audience and finally, the features and performance requirements they were interested in.

# 5 Energy Storage and Protection

# 5.1 Introduction

The tractive system of the electric race car includes the battery, its container and the protection
circuits and devices. The Ground Low Voltage System powers the rest of the vehicle and must be switched
on before the tractive system.
5.2 PART FUNCTIONS
1. The Battery is the part of the tractive system that supplies energy to the motor. It can be
considered the ‘fuel’ of the Electric Race car.
2. The Battery container is a case made of metal designed to keep the battery
(which has very high voltages) isolated from the rest of the vehicle. It prevents damage to the
driver in the highly unlikely case of Electric shock or cell chemistry failure.
3. The Battery Isolation relay is designed to prevent the by cutting off the entire tractive
system from the powertrain in the event of over-voltage or high cell temperatures
4. The Battery Management system (BMS) serves as the diagnostics hub of the entire tractive system and it monitors vital data on the Battery. It also informs the Battery Induction
relay to shut off the tractive system in the case of an emergency
5. The Grounded low voltage (GLV) system is as the on-board power supply for the parts of the car
that are not part of the tractive system and is less than 60VDC
6. Other protection devices include GLV master switch, Isolation Monitoring Device (IMD), Brake
System Plausibility Device (BSPD), Three Shutdown buttons, Brake Over-travel switch, Inertia
Switch, Tractive System measuring points (TSMP), Battery fuses and the
Tractive System Master Switch.

5.3 AIMS AND OBJECTIVES
The initial aims and objectives
- To design a Battery that can provide enough energy for 22km of continuous driving,
braking, turning and acceleration. This is estimated to be at least 5KWh (see calculations below)
- To design the battery such that it can also provide very high bursts of energy over a short
period of time in order to be able to compete in the acceleration event.
- The battery must be as light as possible while delivering sufficient energy i.e. it should have
high energy density
- To design a Battery Container that can withstand the high g forces that it would be
subjected to in racing conditions
Number:
- To design the case in such a way that it acts as the last line of defense in the case of severe failure
- To design a case that seals properly in order to protect the battery from the elements
- To design a Battery Management system (BMS) that is able to monitor the individual cells
reliably and report the data back to the driver and the protective systems.
- Reliability is very important in the BMS because failure of this system would be catastrophic as
failure of subsequent systems would not be properly reported.
- To design an Battery Isolation relay (AIR) that shuts off the entire tractive system when it
receives critical temperature or voltage value from the cells

5.4 PERFORMANCE REQUIREMENTS
• The tractive system must be isolated from the vehicle frame and insulated from the GLV circuit.
• Vehicle frame should be properly grounded
• Cells must be built into segments and stored in a Battery container and insulated from the container.
• The AIR must be a normally open, non-mercury type with a rating higher than the main tractive system fuse. It must completely isolate the container when opened and be insulated from the rest of the battery
• There must be three shutdown switches (One in the cockpit, and one on either side of the vehicle)
• There must be two Master switches to shut down the tractive system and the GLV system
manually
5.5 OPERATIONAL REQUIREMENTS (see calculations for details)
• Battery case should be able to withstand 40g of acceleration.
• Battery should be able to deliver 5kWh of energy
• Battery should be able to discharge at least 17C (17 times its rated discharge capacity) for a short period of time i.e. during sudden acceleration without failure
• Inertia switch must trigger after an 8g impact on the chassis
5.6 MANUFACTURING REQUIREMENTS
• Battery container would be constructed of Steel or Aluminium
• Battery container should be rated to IP65 to survive the rain test. Sealing methods are to be
investigated to attain this rating
• Fireproof material rated to UL94-V0 would be needed for insulation of AIR and fuse
• There should be an Independent power supply for Container Voltage indicator
5.7 CALCULATIONS - Battery Capacity and Power
Endurance course is about 22km long, lasts about 0.35hours and will need at least 4.675KWh of energy to
complete (from 2016 results). Since this is the longest event, we can therefore conclude that a battery
with a 5kWh capacity will be sufficient for this event. Therefore, an average power of 4.675/0.35 = 13.2kW
will be needed. The battery should be able to deliver 13.2kW and have a capacity of 5kWh.
---
The maximum power that can be used by the motor is 85kW. If we use the full power during
the Acceleration event, we would need a cell capable of discharging at 85kW/5kWh=17C.

# 6 Conceptual Design

Regenerative braking power requirement – 63kW (see table below)
Max motor power draw - 80kW

It was decided that it would be more beneficial to make the project as simple as possible i.e. use robust and well tested schemes that have been widely used before. It was for this reason that the regenerative braking system was de-emphasized
Tabular comparison of the three cell choices

| | Turnigy_graphene-4000mAh (advertised) (https://hobbyking.com/en_us/graphene-4000mah-4s-45c-w-xt90.html) | Graphene realistic performance | LG HB2 18650 | Sanyo NCR20700A
| Cells | 4 | 4 | 1 | 1
Ah | Ah | 4 | 4 | 1.5 | 3.1
V | Volts nom | 14.8 | 14.8 | 3.65 | 3.6
A | Max Discharge Current | 180 | 116 | 30 | 30.07
| Discharge C rating | 45 | 29 | 20 | 9.7
| Charge C rating | 10 | 6 | 5.33 | 3
kg | Mass | 0.484 | 0.484 | 0.044 | 0.06
mm | Size | 144 | 144 | 65 | 70.3
mm | | 51 | 51 | 18 | 20.35
mm | | 34 | 34 | 18 | 20.35
| Cost | £41.90 | £41.90 | £2.25 | £3.60
| Energy Derived
W/kg | Power to mass | 122 | 122 | 124 | 186
kg | Total battery wt | 40.9 | 40.9 | 40.2 | 26.9
| # Units for 5kWh | 84 | 84 | 913 | 448
| Car cost | £3,520 | £3,520 | £2,054 | £1,613
| Power derived
kW | Max power per cell | 2.66 | 1.72 | 0.11 | 0.11
| # cells for 80kW | 30 | 47 | 731 | 739
| Cost to meet power | £1,257 | £1,969 | £1,645 | £2,660
kg | Mass | 14.5 | 22.7 | 32.2 | 44.3
| Simple car derived
| # cells | 84 | 84 | 913 | 739
| Cost | £3,520 | £3,520 | £2,054 | £2,660
kg | Mass | 40.9 | 40.9 | 40.2 | 44.3
kW | Max regen power | 49.7 | 29.8 | 26.6 | 24.7
| Assumed regen efficiency | 75% | 75% | 75% | 75%
kW | Braking power available | 66.3 | 39.8 | 35.5 | 33.0
m/s | Assumed average speed | 17.3 | 17.3 | 17.3 | 17.3
kW | Assumed braking power required | 62 | 62 | 62 | 62
| Amount of electrical braking | 80.6% | 48.3% | 43.2% | 40.1%
kWh | Nominal(1C) capacity | 4.9728 | 4.9728 | 4.998675 | 8.24724

Concept 1
Turnigy 4000mAh 4S 45C LiPo (Lithium Polymer) pack is a high capacity cell from Hobbyking. Although the specifications show a very high charge and very high discharge rating, there is evidence online that the cells might be overrated and do not actually perform at advertised specifications. The tests I saw for a different cell reached about 65% of the advertised rating before overheating (a model advertised as 65C performed at a maximum of 41C) so I cut down the advertised ratings in the second tab to better anticipate the real conditions of this cell. It was also given a bad reliability rating in the decision matrix because of this

Concept 2
Sanyo 20700A is a high discharge cell made specifically for electric vehicles. Although it is quite a versatile cell, it was not chosen as it is quite difficult to find it for purchase. Another difficulty associated with it is one that is general to cylindrical cells. The structure makes it quite difficult to attach electrical leads to its terminal as it must be welded. The advantage of cylindrical over pouch
cells is that the construction helps to keep the cell at an ideal pressure.

Concept 3
The LG HB2 is a cheap 18650 cell. The 18650 has been tested in numerous automotive applications (e.g. Tesla Vehicles and other FSAE vehicles) but the drawbacks of the cylindrical cell remain. Connecting it in a 91s10p configuration we get a total rating of 332V,15A (with a maximum burst of up to 300A) which is sufficient for our chosen motor.

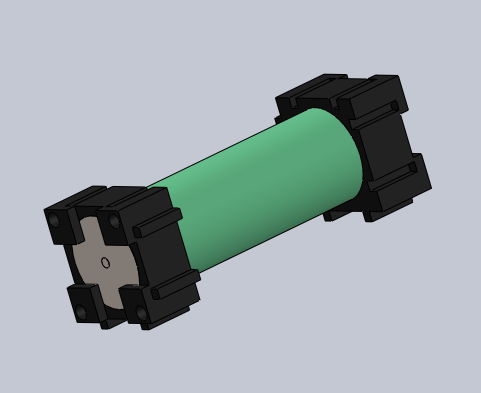
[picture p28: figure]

Figure 3: LG 18650 cell

Decision Matrix

| Concept 1 | Concept 2 | Concept 3
Cost | 7 | 9 | 10
Reliability | 5 | 9 | 8
Weight | 9 | 9 | 8
Ease of Setup | 10 | 7 | 7
| 31 | 34 | 33

From the decision matrix, we can see that the Concept 2 best fulfils our requirements as it is the
lightest cell while being the second cheapest. The only drawback would be in the setup of the cell as
it would be more difficult to assemble it because of the soldering required. This is considered an
acceptable trade-off for the cost and weight.
Buy vs Make Analysis
It would not be practical to make the battery cells, so the best option is to buy.

# 7 Final Design

The design was altered considerably from the initial proposal. Though concept 2 was initally chosen, the parts required were not readily available so the next best concept (3) was chosen and the design altered.

Battery Module
The battery module is assembled by taking eight LG HB2 18650 cells, adding an 18650-plastic spacer and then finally the Cu101 conductor. The module pcb is then screwed in to one side of the module. Eight of these cells are connected in parallel and they collectively make one battery module. There are
120 such modules in the entire battery pack (Making a total of 960 cells).

Each module is in effect a 12A (1.5A*8), 3.6Volt battery and 120 modules (15
per section *8sections) will be connected in series to give us a final pack voltage
of 432V, I=12A (at 1C Discharge, 240A Max. Continuous discharge),
P=5.18kW/18.65MJ.

Section Calculations
EV3.3.3 states that each section must be no greater than 120V, 6MJ.
Our section design here is 3.6V*15=54V /648Wh/ 2.332MJ which meets
the requirements.

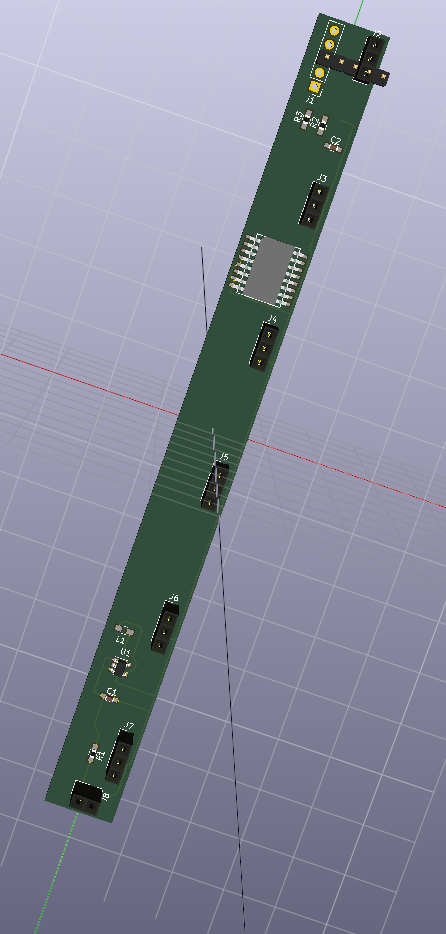
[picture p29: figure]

(a) (b)

Figure 4(a) 3d render of pcb for battery modules (the design requires 90 of these);

(b)Assembled module with battery, plastic sleeve, conductor and pcb


Fig5(a)Assembled Section (b) Sections assembled in Battery Box

Battery box assembly

The battery box will be made of a 4mm thick, 505*458mm Aluminium plate as a
base with four walls (and 300mm high) and a sloping front to facilitate easy maintenance. Internal sections fastened with M8 bolts will divide the box into eight sections and finally four 2.3mm thick external walls (280mm high) fastened with M8 bolts. The internal walls will then be covered with fire retardant formex and 15 modules inserted in each section. The PCB for each section will be inserted in the 32mm gap between the top of the modules and the top of the internal vertical wall. Finally, the top cover will be sealed with gaskets in order to fulfil the rain test requirement.


Figure 6: Battery Box

Battery Management System
Temperature Acquisition Circuit
The temperature sensors will be placed at the end of each cell. The sensor
selected is a Texas Instruments LMT-84 in a TO-92 Package. This will be inserted
into the module PCB which then connects to a module multiplexer. This
multiplexer selects one cell per module and sends the temperature value to the
Analog to Digital Converter (ADC), once the temperature is converted and sent
to the microcontroller, the microcontroller signals to the multiplexer to take the
next cell temperature and this goes on until all six cells in a module are
measured. Since there are 18 modules in each section, there will be three such
ADCs per section. Each ADC is responsible for six modules. The ADCs send the digital information of the cell temperatures to the
Microcontroller using I2C communication. Instead of directly reading all 108 cells
in a section (6 cells * 18 modules) which will require 108 analog pins or 18pcs of
8-channel ADCs, we are able to save space and cost by using a local multiplexer
to switch temperatures.

The LMT84 is a precision CMOS temperature sensor which has a linear Voltage to
temperature behaviour making it superior to NTC sensors (which have nonlinear
behaviour and are very much affected by self-heating). It operates between
1.5V to 5V (VDD)
The TI SN74LV4051A-Q1 is an Automotive rated 8 Channel CMOS multiplexer
that has one output. The switching is done by the microcontroller and all 90
modules will have their local MUX unit which will all be connected by the same
four GPIO pins from the µC. It comes in a compact 8.89*10.63*2.65mm SOIC
package and will be inserted in a PCB just above the modules in the battery box.
2V < VDD <5.5V
The TI ADS7828-Q1 is an Automotive rated 12-bit, 8 Channel Analog to Digital
Converter (ADC) with an I2C communications port and a 50kHz Sampling rate.
It comes in a TSSOP 6.4*5mm package. 2.7V < VDD <5V

Battery Protection
A battery management system composed of TI parts (listed in the BOM submission) monitors each 15-cell section, each section pcb (shown below) can work autonomously to monitor and protect the battery, it will also perform voltage balancing among cells.


Figure 7: Section PCB (*8 for entire design)

# 8 Front line task

The job of Subgroup leader of the Electric Vehicle is to manage the team to make sure the work is being done. The team’s goal was initially to design a class 2 entry for formula student. This was however scaled back as the team had less interest than was initially anticipated. The two team members then set out to design a base on which a future City Racing electric vehicle could be built. Since the most distinguishing part of the Electric vehicle was the powertrain (energy storage + drive system) we decided to work on the battery system for energy storage and the motors to transfer power to the wheels.

We were able to achieve a good initial design that could be further improved upon and tested.

# References

[1] J. J. Eckert, L. C. A. Silva, E. S. Costa, F. M. Santiciolli, F. G. Dedini, and F. C. Corrêa, “Electric vehicle drivetrain optimisation,” IET Electr. Syst. Transp., vol. 7, no. 1, pp. 32–40, 2017.

[2] L. C. S. E. S. C. F. M. S. F. G. D. F. C. C. Jony J. Eckert, "Electric vehicle drivetrain optimisation," IEEE Electr. Syst. Transp., vol. 7, no. 1, pp. 32-40, 2017.

[3] FSAE Regulations; http://www.fsaeonline.com/content/2017_FSAE_Rules

.pdf

[4] D. Seward, Race car design. London: Palgrave, 2014.

[Type text][Type text][Type text]

Formula StudentCITY RACING 20188

Formula StudentCITY RACING 20181

Electric Vehicle Subgroup Group Members Ahmed Abid-Ali Fe-eze Anyafulu Programme & Part: Electrical Engineering Part 4

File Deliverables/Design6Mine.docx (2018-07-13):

Intro

Electric vehicles

greater efficiency

better for environment

better acceleration because o... reference tesla

Set out to build the core of an electric vehicle

my part

1 Introduction

The tractive system of the electric race car includes the battery, its container and the protection
circuits and devices. The Ground Low Voltage System powers the rest of the vehicle and must be switched
on before the tractive system.
PART FUNCTIONS
1. The Battery is the part of the tractive system that supplies energy to the motor. It can be
considered the ‘fuel’ of the Electric Race car.
2. The Battery container is a case made of metal designed to keep the battery
(which has very high voltages) isolated from the rest of the vehicle. It prevents damage to the
driver in the highly unlikely case of Electric shock or cell chemistry failure.
3. The Battery Isolation relay is designed to prevent the by cutting off the entire tractive
system from the powertrain in the event of over-voltage or high cell temperatures
4. The Battery Management system (BMS) serves as the diagnostics hub of the entire tractive
system and it monitors vital data on the Batterys. It also informs the Battery Induction
relay to shut off the tractive system in the case of an emergency
5. The Grounded low voltage (GLV) system is as the on-board power supply for the parts of the car
that are not part of the tractive system and is less than 60VDC
6. Other protection devices include GLV master switch, Isolation Monitoring Device (IMD), Brake
System Plausibility Device (BSPD), Three Shutdown buttons, Brake Over-travel switch, Inertia
Switch, Tractive System measuring points (TSMP), Battery fuses and the
Tractive System Master Switch.

AIMS AND OBJECTIVES
The initial aims and objectives
- To design a Battery that can provide enough energy for 22km of continuous driving,
braking, turning and acceleration. This is estimated to be at least 5KWh (see calculations below)
- To design the battery such that it can also provide very high bursts of energy over a short
period of time in order to be able to compete in the acceleration event.
- The battery must be as light as possible while delivering sufficient energy i.e. it should have
high energy density
- To design a Battery Container that can withstand the high g forces that it would be
subjected to in racing conditions
Number:
- To design the case in such a way that it acts as the last line of defense in the case of severe failure
- To design a case that seals properly in order to protect the battery from the elements
- To design a Battery Management system (BMS) that is able to monitor the individual cells
reliably and report the data back to the driver and the protective systems.
- Reliability is very important in the BMS because failure of this system would be catastrophic as
failure of subsequent systems would not be properly reported.
- To design an Battery Isolation relay (AIR) that shuts off the entire tractive system when it
receives critical temperature or voltage value from the cells

PERFORMANCE REQUIREMENTS (see Appendix for details of Standards)
• The tractive system must be isolated from the vehicle frame and insulated from the GLV circuit.
• Vehicle frame should be properly grounded
• Cells must be built into segments and stored in an Battery container and insulated from the
container.
• The AIR must be a normally open, non-mercury type with a rating higher than the main tractive
system fuse. It must completely isolate the container when opened and be insulated from the rest
of the battery
• There must be three shutdown switches (One in the cockpit, and one on either side of the vehicle)
• There must be two Master switches to shut down the tractive system and the GLV system
manually
OPERATIONAL REQUIREMENTS (see calculations for details)
• Battery case should be able to withstand 40g of acceleration.
• Battery should be able to deliver 5kWh of energy
• Battery should be able to discharge at least 17C (17 times its rated discharge capacity) for a
short period of time i.e. during sudden acceleration without failure
• Inertia switch must trigger after an 8g impact on the chassis
MANUFACTURING REQUIREMENTS
• Battery container would be constructed of Steel or Aluminium
• Battery container should be rated to IP65 to survive the rain test. Sealing methods are to be
investigated to attain this rating
• Fireproof material rated to UL94-V0 would be needed for insulation of AIR and fuse
• There should be an Independent power supply for Container Voltage indicator
CALCULATIONS - Battery Capacity and Power
Endurance course is about 22km long, lasts about 0.35hours and will need at least 4.675KWh of energy to
complete (from 2016 results). Since this is the longest event, we can therefore conclude that a battery
with a 5kWh capacity will be sufficient for this event. Therefore, an average power of 4.675/0.35 = 13.2kW
will be needed. The battery should be able to deliver 13.2kW and have a capacity of 5kWh.
---
The maximum power that can be used by the motor is 85kW. If we use the full power during
the Acceleration event, we would need a cell capable of discharging at 85kW/5kWh=17C.

Concpetual Design

Regenerative braking power requirement – 63kW (see table below)
Max motor power draw - 80kW

It was decided that it would be more beneficial to make the project as simple as possible i.e. use
robust and well tested schemes that have been widely used before. It was for this reason that the
regenerative braking system was de-emphasized
Tabular comparison of the three cell choices

| | Turnigy_graphene-4000mAh (advertised) (https://hobbyking.com/en_us/graphene-4000mah-4s-45c-w-xt90.html) | Graphene realistic performance | LG HB2 18650 | Sanyo NCR20700A
| Cells | 4 | 4 | 1 | 1
Ah | Ah | 4 | 4 | 1.5 | 3.1
V | Volts nom | 14.8 | 14.8 | 3.65 | 3.6
A | Max Discharge Current | 180 | 116 | 30 | 30.07
| Discharge C rating | 45 | 29 | 20 | 9.7
| Charge C rating | 10 | 6 | 5.33 | 3
kg | Mass | 0.484 | 0.484 | 0.044 | 0.06
mm | Size | 144 | 144 | 65 | 70.3
mm | | 51 | 51 | 18 | 20.35
mm | | 34 | 34 | 18 | 20.35
| Cost | £41.90 | £41.90 | £2.25 | £3.60
| Energy Derived
W/kg | Power to mass | 122 | 122 | 124 | 186
kg | Total battery wt | 40.9 | 40.9 | 40.2 | 26.9
| # Units for 5kWh | 84 | 84 | 913 | 448
| Car cost | £3,520 | £3,520 | £2,054 | £1,613
| Power derived
kW | Max power per cell | 2.66 | 1.72 | 0.11 | 0.11
| # cells for 80kW | 30 | 47 | 731 | 739
| Cost to meet power | £1,257 | £1,969 | £1,645 | £2,660
kg | Mass | 14.5 | 22.7 | 32.2 | 44.3
| Simple car derived
| # cells | 84 | 84 | 913 | 739
| Cost | £3,520 | £3,520 | £2,054 | £2,660
kg | Mass | 40.9 | 40.9 | 40.2 | 44.3
kW | Max regen power | 49.7 | 29.8 | 26.6 | 24.7
| Assumed regen efficiency | 75% | 75% | 75% | 75%
kW | Braking power available | 66.3 | 39.8 | 35.5 | 33.0
m/s | Assumed average speed | 17.3 | 17.3 | 17.3 | 17.3
kW | Assumed braking power required | 62 | 62 | 62 | 62
| Amount of electrical braking | 80.6% | 48.3% | 43.2% | 40.1%
kWh | Nominal(1C) capacity | 4.9728 | 4.9728 | 4.998675 | 8.24724

Concept 1
Turnigy 4000mAh 4S 45C LiPo (Lithium Polymer) pack is a high capacity cell from Hobbyking.
Although the specifications show a very high charge and very high discharge rating, there is evidence
online that the cells might be overrated and do not actually perform at advertised specifications. The
tests I saw for a different cell reached about 65% of the advertised rating before overheating (a
model advertised as 65C performed at a maximum of 41C) so I cut down the advertised ratings in
the second tab to better anticipate the real conditions of this cell. It was also given a bad reliability
rating in the decision matrix because of this
Concept 2
Sanyo 20700A is a high discharge cell made specifically for electric vehicles. Although it is quite a
versatile cell, it was not chosen as it is quite difficult to find it for purchase. Another difficulty
associated with it is one that is general to cylindrical cells. The structure makes it quite difficult to
attach electrical leads to its terminal as it must be welded. The advantage of cylindrical over pouch
cells is that the construction helps to keep the cell at an ideal pressure.
Concept 3
The LG HB2 is a cheap 18650 cell. The 18650 has been tested in numerous automotive applications
(e.g. Tesla Vehicles and other FSAE vehicles) but the drawbacks of the cylindrical cell remain.
Connecting it in a 91s10p configuration we get a total rating of 332V,15A (with a maximum burst of
up to 300A) which is sufficient for our chosen motor.


Decision Matrix

| Concept 1 | Concept 2 | Concept 3
Cost | 7 | 9 | 10
Reliability | 5 | 9 | 8
Weight | 9 | 9 | 8
Ease of Setup | 10 | 7 | 7
| 31 | 34 | 33

From the decision matrix, we can see that the Concept 2 best fulfils our requirements as it is the
lightest cell while being the second cheapest. The only drawback would be in the setup of the cell as
it would be more difficult to assemble it because of the soldering required. This is considered an
acceptable trade-off for the cost and weight.
Buy vs Make Analysis
It would not be practical to make the battery cells, so the best option is to buy.

Final Design

The design was altered considerably from the initial proposal. Though concept 2 was initally chosen, the parts required were not readily available so the next best concept (3) was chosen and the design altered.

Mechanical Configuration

Battery Module
The battery module is assembled by taking eight LG HB2 18650 cells, adding an 18650-plastic spacer and then finally the Cu101 conductor. The module pcb is then screwed in to one side of the module. Eight of these cells are connected in parallel and they collectively make one battery module. There are
120 such modules in the entire battery pack (Making a total of 960 cells).

Each module is in effect a 12A (1.5A*8), 3.6Volt battery and 120 modules (15
per section *8sections) will be connected in series to give us a final pack voltage
of 432V, I=12A (at 1C Discharge, 240A Max. Continuous discharge),
P=5.18kW/18.65MJ.

Section Calculations
EV3.3.3 states that each section must be no greater than 120V, 6MJ.
Our section design here is 3.6V*15=54V /648Wh/ 2.332MJ which meets
the requirements.


3d render of pcb for battery modules (the design requires 90 of these);

Assembled module with battery, plastic sleeve, conductor and pcb


Assembled Section Sections assembled in Battery Box

Battery box assembly

The battery box will be made of a 4mm thick, 505*458mm Aluminium plate as a
base with four walls (and 300mm high) and a sloping front to facilitate easy maintenance. Internal sections fastened with M8 bolts will divide the box into eight
sections and finally four 2.3mm thick external walls (280mm high) fastened with M8 bolts. The internal walls will then be covered with fire retardant formex and 15 modules inserted in each section. The PCB for each section will be inserted in the 32mm gap between the top of the modules and the top of the internal vertical wall. Finally, the top cover will be sealed with gaskets in order to fulfil the rain test requirement.


Battery Management System
Temperature Acquisition Circuit
The temperature sensors will be placed at the end of each cell. The sensor
selected is a Texas Instruments LMT-84 in a TO-92 Package. This will be inserted
into the module PCB which then connects to a module multiplexer. This
multiplexer selects one cell per module and sends the temperature value to the
Analog to Digital Converter (ADC), once the temperature is converted and sent
to the microcontroller, the microcontroller signals to the multiplexer to take the
next cell temperature and this goes on until all six cells in a module are
measured. Since there are 18 modules in each section, there will be three such
ADCs per section. Each ADC is responsible for six modules. The ADCs send the digital information of the cell temperatures to the
Microcontroller using I2C communication. Instead of directly reading all 108 cells
in a section (6 cells * 18 modules) which will require 108 analog pins or 18pcs of
8-channel ADCs, we are able to save space and cost by using a local multiplexer
to switch temperatures.

The LMT84 is a precision CMOS temperature sensor which has a linear Voltage to
temperature behaviour making it superior to NTC sensors (which have nonlinear
behaviour and are very much affected by self-heating). It operates between
1.5V to 5V (VDD)
The TI SN74LV4051A-Q1 is an Automotive rated 8 Channel CMOS multiplexer
that has one output. The switching is done by the microcontroller and all 90
modules will have their local MUX unit which will all be connected by the same
four GPIO pins from the µC. It comes in a compact 8.89*10.63*2.65mm SOIC
package and will be inserted in a PCB just above the modules in the battery box.
2V < VDD <5.5V
The TI ADS7828-Q1 is an Automotive rated 12-bit, 8 Channel Analog to Digital
Converter (ADC) with an I2C communications port and a 50kHz Sampling rate.
It comes in a TSSOP 6.4*5mm package. 2.7V < VDD <5V

Battery Protection
A battery management system composed of TI parts (listed in the BOM submission) monitors each 15-cell section, each section pcb (shown below) can work autonomously to monitor and protect the battery, it will also perform voltage balancing among cells.


Section PCB (*8 for entire design)

Front line task

The job of Subgroup leader of the Electric Vehicle was initially to design a class 2 entry for formula student. This was however scaled back as the team had less interest than initially anticipated. The two team members then set out to design a base on which future CityRacing teBMS could build. Since the most distinguishing part of the Electric vehicle was the powertrain(energy storage + drive system) we decided to work on the battery system for energy storage and the motors to transfer power to the wheels.

We were able to achieve a good initial design that could be further improved upon and tested

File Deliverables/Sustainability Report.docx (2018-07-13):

Sustainability Report

A Sustainability report was carried out on the battery box and the assembled battery sections which will go into the box (the bricks). This was done using the Solidworks Sustainability function. The box was set to be manufactured and used in Europe while the battery section was set to be manufactured in Asia and used in Europe. The results are shown below:

Map

| Manufacturing Region The choice of manufacturing region determines the energy sources and technologies used in the modeled material creation and manufacturing steps of the product’s life cycle.
| Use Region The use region is used to determine the energy sources consumed during the product’s use phase (if applicable) and the destination for the product at its end-of-life. Together with the manufacturing region, the use region is also used to estimate the environmental impacts associated with transporting the product from its manufacturing location to its use location.

Sustainability report for battery box

Environmental Impact (calculated using TRACI impact assessment methodology)
Carbon Footprint Material: 990 kg CO2e Manufacturing: 45 kg CO2e Use: 0.00 kg CO2e Transportation: 23 kg CO2e End of Life: 130 kg CO2e 1200 kg CO2e | Total Energy Consumed Material: 1.2E+4 MJ Manufacturing: 750 MJ Use: 0.00 MJ Transportation: 350 MJ End of Life: 95 MJ 1.3E+4 MJ
Air Acidification Material: 320 mol H⁺ e Manufacturing: 15 mol H⁺ e Use: 0.00 mol H⁺ e Transportation: 9.4 mol H⁺ e End of Life: 5.1 mol H⁺ e 350 mol H⁺ e | Water Eutrophication Material: 0.086 kg N e Manufacturing: 5.4E-3 kg N e Use: 0.00 kg N e Transportation: 9.0E-3 kg N e End of Life: 0.033 kg N e 0.133 kg N e

Material Financial Impact | 176.10 USD

Comments

Component Environmental Impact

Top Ten Components Contributing Most to the Four Areas of Environmental Impact

Component | Carbon | | | | | | | | | | Water | | | | | | | | | | Air | | | | | | | | | Energy
box_TopCover | 37 | | | | | | | | | | 3.3E-3 | | | | | | | | | | 11 | | | | | | | | | 460
box_base | 33 | | | | | | | | | | 2.9E-3 | | | | | | | | | | 10 | | | | | | | | | 400
box_back | 20 | | | | | | | | | | 1.8E-3 | | | | | | | | | | 6.3 | | | | | | | | | 250
box_side | 20 | | | | | | | | | | 1.8E-3 | | | | | | | | | | 6.2 | | | | | | | | | | 250
box_sidemirrored | 20 | | | | | | | | | | 1.7E-3 | | | | | | | | | | 6.1 | | | | | | | | | 240
box_frontdivider | 17 | | | | | | | | | | 1.5E-3 | | | | | | | | | | 5.4 | | | | | | | | | 220
box_inner | 12 | | | | | | | | | | 1.1E-3 | | | | | | | | | | 3.9 | | | | | | | | | 150
box_front | 5.7 | | | | | | | | | | 5.0E-4 | | | | | | | | | | 1.8 | | | | | | | | | 71

Sustainability Report for Section Assembly
Model Name: | | SectionAssembly | | | | Weight: | 21597.07 g
| | | | | | Built to last: | 5.0 year
| | | | | | Duration of use: | 5.0 year
Carbon Footprint Material: 280 kg CO2e Manufacturing: 91 kg CO2e Use: 0.00 kg CO2e Transportation: 6.2 kg CO2e End of Life: 12 kg CO2e 390 kg CO2e | | | | | Total Energy Consumed Material: 3700 MJ Manufacturing: 910 MJ Use: 0.00 MJ Transportation: 82 MJ End of Life: 8.7 MJ 4700 MJ
Air Acidification Material: 57 mol H⁺ e Manufacturing: 61 mol H⁺ e Use: 0.00 mol H⁺ e Transportation: 8.5 mol H⁺ e End of Life: 0.408 mol H⁺ e 130 mol H⁺ e | | | | | Water Eutrophication Material: 0.359 kg N e Manufacturing: 0.023 kg N e Use: 0.00 kg N e Transportation: 5.2E-3 kg N e End of Life: 3.7E-3 kg N e 0.391 kg N e

Material Financial Impact | 102.70 USD

Sustainability Report
Model Name: | | SectionAssembly | | | Weight: | 21597.07 g
| | | | | Built to last: | 5.0 year
| | | | | Duration of use: | 5.0 year

Component Environmental Impact

Top Ten Components Contributing Most to the Four Areas of Environmental Impact

Component | Carbon | | | | | | Water | | | | | | | Air | | | | | | Energy
DummyPCBForSection | 1.3 | | | | | | 3.2E-4 | | | | | | | 0.598 | | | | | | 18
HB2 | 0.520 | | | | | | 5.0E-4 | | | | | | | 0.164 | | | | | | 6.0
DummyPCB | 0.444 | | | | | | 1.1E-4 | | | | | | | 0.199 | | | | | | 6.0
CopperConductor | 0.034 | | | | | | 9.3E-6 | | | | | | | 0.014 | | | | | | 0.439
pan slot head_am | 7.5E-3 | | | | | | 3.7E-5 | | | | | | | 1.4E-3 | | | | | | 0.074
EndCap | 0.016 | | | | | | 5.2E-6 | | | | | | | 5.1E-3 | | | | | | 0.285
EndCapWithM3 | 0.015 | | | | | | 4.8E-6 | | | | | | | 4.8E-3 | | | | | | 0.266

It should be noted that these are just rough estimates of the Environmental Impact of the parts. For example the battery itself was analysed as a stainless steel part as there is no specific battery material available.

[Type text][Type text][Type text]

Formula StudentCITY RACING 20183

Formula StudentCITY RACING 20181

Name: Fe-eze Anyafulu Programme & Part: Electrical Engineering Part 4 Project Role: Electric Vehicle Battery System Subgroup: Electric Vehicle Frontline Task: EV Team Lead

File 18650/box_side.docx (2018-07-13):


[company logo here]
[company name here] | | | | [city, state here] | | [company url here] | | | | | | | Sustainability Report

[name] ∙ | [title] | ∙ ∙ [email address] ∙ | (###) ###-####


| | | | | | | | | | | Model Name: box_side Material: 6061 Alloy Recycled content: 0.00 % Weight: 1533.73 g Manufacturing process: Sheetmetal Surface Area: 2.90E+5 mm² Built to last: 5.0 year Duration of use: 5.0 year


| | | | | | | | | | | Manufacturing Region The choice of manufacturing region determines the energy sources and technologies used in the modeled material creation and manufacturing steps of the product’s life cycle.
| | | | | | | | | | | Use Region The use region is used to determine the energy sources consumed during the product’s use phase (if applicable) and the destination for the product at its end-of-life. Together with the manufacturing region, the use region is also used to estimate the environmental impacts associated with transporting the product from its manufacturing location to its use location.

Summary

Learn more about Life Cycle Assessment (http://www.solidworks.com/sustainabilityinfo)

Sustainability Report
| Model Name: | | box_side | | Material: | | 6061 Alloy | | | | | Weight: | | 1533.73 g | Manufacturing process:
| | | | | | | | | | | | Surface Area: | | 2.90E+5 mm² | Sheetmetal
| | | | | Recycled content: | | 0.00 % | | | | | Built to last: | | 5.0 year
| | | | | | | | | | | | Duration of use: | | 5.0 year

Material | 6061 Alloy | 0.00 %
Material Unit Cost | 2.20 USD/kg
| Manufacturing Region: Europe Process: Sheetmetal Electricity consumption: 0.715 kWh/lbs Natural gas consumption: 2900 BTU/lbs Scrap rate: 0.430 % Built to last: 5.0 year Part is painted: No Paint | | | | | | | | Use Region: Europe Duration of use: 5.0 year
| Transportation Truck distance: 1900 km Train distance: 0.00 km Ship distance: 0.00 km Airplane Distance: 0.00 km | | | | | | | | End of Life Recycled: 25 % Incinerated: 24 % Landfill: 51 %

Comments
| Click here for alternative units such as ‘Miles Driven in a Car’ (http://www.solidworks.com/plugins/sustainability/calculator.htm?LANG=en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)

Sustainability Report
| Model Name: | | box_side | | Material: | | | 6061 Alloy | | | | Weight: | | 1533.73 g | Manufacturing process:
| | | | | | | | | | | | Surface Area: | | 2.90E+5 mm² | Sheetmetal
| | | | | Recycled content: | | | 0.00 % | | | | Built to last: | | 5.0 year
| | | | | | | | | | | | Duration of use: | | 5.0 year

Environmental Impact (calculated using TRACI impact assessment methodology)
| Carbon Footprint Material: 18 kg CO2e Manufacturing: 0.931 kg CO2e Transportation: 0.140 kg CO2e End of Life: 0.491 kg CO2e 20 kg CO2e | | | | | | | | Total Energy Consumed Material: 230 MJ Manufacturing: 17 MJ Transportation: 2.1 MJ End of Life: 0.500 MJ 250 MJ
| Air Acidification Material: 5.9 mol H⁺ e Manufacturing: 0.218 mol H⁺ e Transportation: 0.049 mol H⁺ e End of Life: 0.031 mol H⁺ e 6.2 mol H⁺ e | | | | | | | | Water Eutrophication Material: 1.6E-3 kg N e Manufacturing: 7.6E-5 kg N e Transportation: 5.0E-5 kg N e End of Life: 3.2E-5 kg N e 1.8E-3 kg N e

Material Financial Impact | 3.40 USD

Comments
| Click here for alternative units such as ‘Miles Driven in a Car’ (http://www.solidworks.com/plugins/sustainability/calculator.htm?LANG=en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)

Sustainability Report


Sustainability Report

Glossary

Air Acidification - Sulfur dioxide, nitrous oxides other acidic emissions to air cause an increase in the acidity of rainwater, which in turn acidifies lakes and soil. These acids can make the land and water toxic for plants and aquatic life. Acid rain can also slowly dissolve manmade building materials such as concrete. This impact is typically measured in units of either kg sulfur dioxide equivalent (SO2), or moles H+ equivalent.

Carbon Footprint - Carbon-dioxide and other gasses which result from the burning of fossil fuels accumulate in the atmosphere which in turn increases the earth’s average temperature. Carbon footprint acts as a proxy for the larger impact factor referred to as Global Warming Potential (GWP). Global warming is blamed for problems like loss of glaciers, extinction of species, and more extreme weather, among others.

Total Energy Consumed - A measure of the non-renewable energy sources associated with the part’s lifecycle in units of megajoules (MJ). This impact includes not only the electricity or fuels used during the product’s lifecycle, but also the upstream energy required to obtain and process these fuels, and the embodied energy of materials which would be released if burned. Total Energy Consumed is expressed as the net calorific value of energy demand from non-renewable resources (e.g. petroleum, natural gas, etc.). Efficiencies in energy conversion (e.g. power, heat, steam, etc.) are taken into account.

Water Eutrophication - When an over abundance of nutrients are added to a water ecosystem, eutrophication occurs. Nitrogen and phosphorous from waste water and agricultural fertilizers causes an overabundance of algae to bloom, which then depletes the water of oxygen and results in the death of both plant and animal life. This impact is typically measured in either kg phosphate equivalent (PO4) or kg nitrogen (N) equivalent.

Life Cycle Assessment (LCA) - This is a method to quantitatively assess the environmental impact of a product throughout its entire lifecycle, from the procurement of the raw materials, through the production, distribution, use, disposal and recycling of that product.

Material Financial Impact - This is the financial impact associated with the material only. The mass of the model is multiplied by the financial impact unit

(units of currency/units of mass) to calculate the financial impact (in units of currency).

Learn more about Life Cycle Assessment (http://www.solidworks.com/sustainabilityinfo)

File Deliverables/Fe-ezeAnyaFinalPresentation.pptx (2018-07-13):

## Electric Vehicle Subgroup


Ahmed Abid-Ali
Fe-eze Anyafulu
MEng Electrical Engineering Part 4
City, University of London
11 June 2018

## Introduction

- Goals
- To design a battery and battery management system for the FSAE vehicle that can provide enough energy for 22km of continuous driving
- To design a battery that can provide high bursts of energy over short periods
- Keep the battery as light and low cost as possible while delivering enough energy
- Design a Battery Management System that can reliably protect the battery

## Conceptual Design

. | | Graphene realistic performance | LG HB2 18650 | Sanyo NCR20700A
| Cells | 4 | 1 | 1
Ah | Ah | 4 | 1.5 | 3.1
V | Volts nom | 14.8 | 3.65 | 3.6
A | Max Discharge Current | 116 | 30 | 30.07
| Discharge C rating | 29 | 20 | 9.7
| Charge C rating | 6 | 5.33 | 3
kg | Mass | 0.484 | 0.044 | 0.06
mm | Size | 144 | 65 | 70.3
mm | | 51 | 18 | 20.35
mm | | 34 | 18 | 20.35
| Cost | £41.90 | £2.25 | £3.60
| Energy Derived
W/kg | Power to mass | 122 | 124 | 186
kg | Total battery wt | 40.9 | 40.2 | 26.9
| # Units for 5kWh | 84 | 913 | 448
| Car cost | £3,520 | £2,054 | £1,613
| Power derived
kW | Max power per cell | 1.72 | 0.11 | 0.11
| # cells for 80kW | 47 | 731 | 739
| Cost to meet power | £1,969 | £1,645 | £2,660
kg | Mass | 22.7 | 32.2 | 44.3
| Simple car derived
| # cells | 84 | 913 | 739
| Cost | £3,520 | £2,054 | £2,660
kg | Mass | 40.9 | 40.2 | 44.3
kW | Max regen power | 29.8 | 26.6 | 24.7
| Assumed regen efficiency | 75% | 75% | 75%
kW | Braking power available | 39.8 | 35.5 | 33.0
m/s | Assumed average speed | 17.3 | 17.3 | 17.3
kW | Assumed braking power required | 62 | 62 | 62
| Amount of electrical braking | 48.3% | 43.2% | 40.1%
kWh | Nominal(1C) capacity | 4.9728 | 4.998675 | 8.24724


| Concept 1 | Concept 2 | Concept 3
Cost | 7 | 9 | 10
Reliability | 5 | 9 | 8
Weight | 9 | 9 | 8
Ease of Setup | 10 | 7 | 7
| 31 | 34 | 33

Capacity Calculation
Endurance course is about 22km long, lasts about 0.35hours and will need at least 4.675KWh of energy to complete (from 2016 results). Since this is the longest event, we can therefore conclude that a battery with a 5kWh capacity will be sufficient for this event. Therefore, an average power of 4.675/0.35 = 13.2kW will be needed. The battery should be able to deliver 13.2kW and have a capacity of 5kWh.
Max Discharge Calculation
Max power - 80kW.
If we use the full power during the Acceleration event, we would need a cell capable of discharging at 80kW/5kWh=16C.

## Design: Battery and Battery box


- Battery box - 4mm thick, 505*458mm Aluminium plate as a base with four walls (and 300mm high) and a sloping front to facilitate easy maintenance.
- Internal sections to divide the box into eight sections and The internal walls to be covered with fire retardant formex and one brick inserted in each section.
- PCB for each section will be inserted in the 32mm gap between the top of the modules and the top of the internal vertical wall.
- Top cover sealed with gaskets in order to fulfil the rain test requirement.

- 8 cells form a string - 12A, 3.6V
- 12 strings form a brick
- 8 brick sections in the battery box
- Final pack characteristics
- 432V, 12A (1C), 240A Max. discharge

## Design: Battery Management System


- 1st PCB custom designed around TI parts to link 8 parallel cells and perform temperature monitoring.
- LMT-84 temp sensor
- SN74xx ADC for temperature muxing
- 2nd PCB is a 15-cell voltage monitor with a FET driver from TI


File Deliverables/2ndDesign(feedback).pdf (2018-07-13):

## Design II – Conceptual Design


Formula Student | CITY RACING 2018 | 1
Name: | Fe-eze Anyafulu
Programme & Part: Electrical & Electronics Eng. Part 4
Project Role: | Tractive System
Subgroup: | Electric Vehicle
Frontline Task: | Electric Vehicle Project Manager

Morphological chart - different options
| Concept 1 | Concept 2 | Concept 3
Cell Structure

Assembly Concept

Regenerative braking power requirement – 63kW (see table below)
Max motor power draw - 80kW (Emrax 208)
It was decided that it would be more beneficial to make the project as simple as possible i.e. use robust and well tested schemes that have been widely used before. It was for this reason that the regenerative braking system was de-emphasized

Tabular comparison of the three cell choices
SI Unit | | Turnigy_graphene-4000mAh (advertised) (https://hobbyking.com/en_us/graphene-4000mah-4s-45c-w-xt90.html) | Turnigy Graphene realistic performance | LG HB2 18650 | Sanyo NCR20700A
| Cells | 4 | 4 | 1 | 1
Ah | Ah | 4 | 4 | 1.5 | 3.1
V | Volts nom | 14.8 | 14.8 | 3.65 | 3.6

A | Max Discharge Current | 180 | 116 | 30 | 30.07
| Discharge C rating | 45 | 29 | 20 | 9.7
| Charge C rating | 10 | 6 | 5.33 | 3
kg | Mass | 0.484 | 0.484 | 0.044 | 0.06
mm | Size | 144 | 144 | 65 | 70.3
mm | | 51 | 51 | 18 | 20.35
mm | | 34 | 34 | 18 | 20.35
| Cost | £41.90 | £41.90 | £3.00 | £3.60
| Energy Derived
W/kg | Power to mass | 122 | 122 | 124 | 186
kg | Total battery wt | 40.9 | 40.9 | 40.2 | 26.9
| # Units for 5kWh | 84 | 84 | 913 | 448
| Car cost | £3,520 | £3,520 | £2,739 | £1,613
| Power derived
kW | Max power per cell | 2.66 | 1.72 | 0.11 | 0.11
| # cells for 80kW | 30 | 47 | 731 | 739
| Cost to meet power | £1,257 | £1,969 | £2,193 | £2,660
kg | Mass | 14.5 | 22.7 | 32.2 | 44.3
| Simple car derived
| # cells | 84 | 84 | 913 | 739
| Cost | £3,520 | £3,520 | £2,739 | £2,660
kg | Mass | 40.9 | 40.9 | 40.2 | 44.3
kW | Max regen power | 49.7 | 29.8 | 26.6 | 24.7
| Assumed regen efficiency | 75% | 75% | 75% | 75%

Braking power available; Assumed average speed; Assumed braking power required; Amount of electrical braking

kWh Nominal(1C)
capacity
4.9728 | 4.9728 | 4.998675 | 8.24724

Concept 1
Turnigy 4000mAh 4S 45C LiPo (Lithium Polymer) pack is a high capacity cell from Hobbyking. Although the specifications show a very high charge and very high discharge rating, there is evidence online that the cells might be overrated and do not actually perform at advertised specifications. The tests I saw for a different cell reached about 65% of the advertised rating before overheating (a model advertised as 65C performed at a maximum of 41C) so I cut down the advertised ratings in the second tab to better anticipate the real conditions of this cell. It was also given a bad reliability rating in the decision matrix because of this

Concept 2
Sanyo 20700A is a high discharge cell made specifically for electric vehicles. Although it is quite a versatile cell, it was not chosen as it is quite difficult to find it for purchase. Another difficulty associated with it is one that is general to cylindrical cells. The structure makes it quite difficult to attach electrical leads to its terminal as it must be welded. The advantage of cylindrical over pouch cells is that the construction helps to keep the cell at an ideal pressure.

Concept 3
The LG HB2 is a cheap 18650 cell. The 18650 has been tested in numerous automotive applications (e.g. Tesla Vehicles and other FSAE vehicles) but the drawbacks of the cylindrical cell remain. Connecting it in a 91s10p configuration we get a total rating of 332V,15A (with a maximum burst of up to 300A) which is sufficient for our chosen motor.

Decision Matrix
| Concept 1 | Concept 2 | Concept 3
Cost | 7 | 9 | 10
Reliability | 5 | 9 | 8
Weight | 9 | 9 | 8
Ease of Setup | 10 | 7 | 7
| 31 | 34 | 33

From the decision matrix, we can see that the Concept 2 best fulfils our requirements as it is the lightest cell while being the second cheapest. The only drawback would be in the setup of the cell as it would be more difficult to assemble it because of the soldering required. This is considered an


acceptable trade-off for the cost and weight.

Buy vs Make Analysis
It would not be practical to make the battery cells, so the best option is to buy.

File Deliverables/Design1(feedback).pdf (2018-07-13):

Number:

Name: Fe-eze Anyafulu
Programme: MEng Electrical and Electronics Engineering Part: 4
Project Role: Electric Vehicle Project Manager
Subgroup: Electric Vehicle

## Design I – Product Design Specifications for Electric Vehicle Tractive System

FOREWORD
The tractive system of the electric race car includes the accumulator, its container and the protection circuits and devices. The Ground Low Voltage System powers the rest of the vehicle and must be switched on before the tractive system.
PART FUNCTIONS
1. The Accumulator is the part of the tractive system that supplies energy to the motor. It can be considered the ‘fuel’ of the Electric Race car.
2. The Accumulator container is a sturdy case made of metal designed to keep the accumulator (which has very high voltages) isolated from the rest of the vehicle. It prevents damage to the driver in the highly unlikely case of Electric shock or cell chemistry failure.
3. The Accumulator Induction relay is designed to prevent the by cutting off the entire tractive system from the powertrain in the event of over-voltage or high cell temperatures
4. The Accumulator Management system (AMS) serves as the diagnostics hub of the entire tractive system and it monitors vital data on the Accumulators. It also informs the Accumulator Induction relay to shut off the tractive system in the case of an emergency
5. The Grounded low voltage (GLV) system is as the on-board power supply for the parts of the car that are not part of the tractive system and is less than 60VDC
6. Other protection devices include GLV master switch, Isolation Monitoring Device (IMD), Brake System Plausibility Device (BSPD), Three Shutdown buttons, Brake Over-travel switch, Inertia Switch, Tractive System measuring points (TSMP), Accumulator fuses and the Tractive System Master Switch.
INTRODUCTION
The aims and objectives are:


- To design an Accumulator that can provide enough energy for 22km of continuous driving, braking, turning and acceleration. This is estimated to be at least 5KWh (see calculations below)
- To design the accumulator such that it can also provide very high bursts of energy over a short period of time in order to be able to compete in the acceleration event.
- The accumulator must be as light as possible while delivering sufficient energy i.e. it should have high energy density
- To design an Accumulator Container that can withstand the high g forces that it would be subjected to in racing conditions

Number:

- To design the case in such a way that it acts as the last line of defence in the case of severe failure
- To design a case that seals properly in order to protect the accumulator from the elements
- To design an Accumulator Management system (AMS) that is able to monitor the individual cells reliably and report the data back to the driver and the protective systems.
- Reliability is very important in the AMS because failure of this system would be catastrophic as failure of subsequent systems would not be properly reported.
- To design an Accumulator Insulation relay (AIR) that shuts off the entire tractive system when it receives critical temperature or voltage value from the cells

PERFORMANCE REQUIREMENTS (see Appendix for details of Standards)
- The tractive system must be isolated from the vehicle frame and insulated from the GLV circuit.
- Vehicle frame should be properly grounded
- Cells must be built into segments and stored in an Accumulator container and insulated from the container.
- The AIR must be a normally open, non-mercury type with a rating higher than the main tractive system fuse. It must completely isolate the container when opened and be insulated from the rest of the accumulator
- There must be three shutdown switches (One in the cockpit, and one on either side of the vehicle)
- There must be two Master switches to shut down the tractive system and the GLV system manually

OPERATIONAL REQUIREMENTS (see calculations for details)
- Accumulator case should be able to withstand 40g of acceleration.
- Accumulator should be able to deliver 5kWh of energy


- Accumulator should be able to discharge at least 17C (17 times its rated discharge capacity) for a short period of time i.e. during sudden acceleration without failure
- Inertia switch must trigger after an 8g impact on the chassis
MANUFACTURING REQUIREMENTS
- Accumulator container would be constructed of Steel or Aluminium
- Accumulator container should be rated to IP65 to survive the rain test. Sealing methods are to be investigated in order to attain this rating
- Fireproof material rated to UL94-V0 would be needed for insulation of AIR and fuse
- There should be an Independent power supply for Container Voltage indicator

CALCULATIONS - Accumulator Capacity and Power


Endurance course is about 22km long, lasts about 0.35hours and will need at least 4.675KWh of energy to complete (from 2016 results). Since this is the longest event, we can therefore conclude that a battery with a 5kWh capacity will be sufficient for this event. Therefore, an average power of 4.675/0.35 = 13.2kW will be needed. The accumulator should be able to deliver 13.2kW and have a capacity of 5kWh.
The maximum power that can be used by the motor is 85kW. If we use the full power during the Acceleration event, we would need a cell capable of discharging at 85kW/5kWh=17C.

Number:

## APPENDIX - All Relevant Standards and Constraints

General tractive system
- The tractive system must be fully isolated from the frame of the vehicle | EV1.2.3, EV4.1.3
- GLV and tractive circuits must be insulated by fireproof material or 30mm of air (for V>200VDC) | EV1.2.7, EV4.1.5
- All parts of the vehicle within 100mm of any tractive system or GLV component must be grounded
Tractive System Accumulator
- The target weight of the accumulator is 40kg
- It can be composed of any type of cell chemistry except molten salt, thermal batteries and fuel cells. Early investigation points to LiFePO4 as the appropriate cell chemistry for this. This will be investigated further in the next report | EV3.1.1
- All cells must be built into accumulator segments and enclosed in an accumulator container | EV3.2.1, EV1.1.5
- The poles of each cell must be isolated from the accumulator container with an insulated material rated for maximum tractive system voltage | EV3.3.1
- Connecting the high current path of the cell by soldering is prohibited, except to the AMS which is a low voltage monitoring system | EV3.3.7
Accumulator Container
- Each container must be removable from the car while remaining rules compliant | EV3.2.4
- Each Accumulator container must have at least one fuse and two AIRs | EV3.3.2
- The outside of the container must have a low resistance connection to the GLV system ground | EV3.3.1, EV4.3.1
- Maintenance plugs must be included to isolate the cell segments such that each segment has less than 120VDC and 6MJ. These plugs must automatically separate the segments whenever they are opened, must be non-conductive on surfaces without electrical connections, must contain a locking feature to prevent it from becoming loose and must be impossible to connect in any other configuration than intended | EV3.3.3, EV3.4.10
- Each Container segment must be electrically insulated from the others by a suitable material on the sides and top | EV3.3.4
- EVERY wire used in the accumulator container must be rated to the maximum voltage | EV3.3.8
- Each container must have a prominent indicator that illuminates when a voltage of 60VDC is present at the vehicle end of the AIR. This indicator must be electronically hardwired and be directly activated by the Voltage present. This indicator must always work regardless of connection to the GLV or lack of it. | EV3.3.9, EV3.3.10, EV3.3.11
- Accumulator container Dimensions Exterior Vertical Wall – 0.9mm (Steel) or 2.3mm (Aluminium) Thick. Interior Vertical Walls – Height must be at least 75% of exterior vertical walls, 0.9mm (Steel) or 2.3mm (Aluminium) Thick. Floor – 1.25mm steel or 3.2mm Aluminium Thick | EV3.4.6

Number:

Lid/Cover – 0.9mm (Steel) or 2.3mm (Aluminium) Thick. Interior Vertical Walls serve to divide Accumulator into sections with a maximum of 12kg per section

- There should be at least two fasteners between the floor and any vertical wall and three fasteners between the vertical walls of any sections that weigh more than 8kg. All fasteners should be 6mm metric grade 8.8 fasteners
- Accumulator containershould be able to withstand 40g of longitudinal acceleration, 40g of Lateral Acceleration and 20g of Vertical acceleration. | EV3.4.7
- Container must be attached to main chassis structure by at least 10 1.6mm Steel brackets or 4mm Aluminium brackets. Each bracket must be able to withstand 20kN in any direction and must have at least one 8.8mm Metric grade fastener | EV3.4.8

Accumulator Management System
- It must constantly measure the cell voltage of every cell (or every block in the case of parallel cell connections) whenever the tractive system is active or charging to make sure cells are within the max and min accepted voltages specified in the data sheet. | EV3.5.1, EV3.5.2
- It must continuously monitor the temperatures of at least 30% of the cells provided they are evenly distributed in the accumulator and keep cell temperatures measured below 60degC or data sheet specifications (whichever is lower). Temperature sensor must be less than 10mm from the negative end of the cell | EV3.5.3, EV3.6.6
- It must shut down the tractive system by opening the AIRs if critical voltage or critical temperature values are reached. A Red LED must light up in the cockpit to confirm shutdown | EV3.6.7

Grounded Low Voltage (GLV) System
- GLV must be less than 60VDC or 25VAC RMS, galvanically isolated from the tractive system and grounded to the chassis. | EV1.1.1, EV1.1.3, EV1.2.4, EV1.2.5, EV1.2.6, EV1.2.7, EV4.1.3
- GLV must be powered on first before the tractive system can be powered on. Any GLV failure must immediately shutdown the tractive system | EV1.2.10
- All GLV batteries must be securely attached to the frame and insulated at the live terminal | EV3.7.1, EV 3.7.3
- GLV must have a rigid, fire retardant casing, a firewall that protects the driver and overcurrent protection | IC4.4.4, EV3.7.4
Accumulator Isolation Relay
- It must be a normally open, non-mercury type with a rating higher than the main tractive system fuse | EV3.5.2
- It must completely isolate the Accumulator such that once it is open, no High Voltage may be present outside the container

Number:

- The AIR and the main fuse must be separated by an electrically insulated and fireproof material from the rest of the accumulator. This material should be rated to ULV94-V0 | EV3.3.5
Other Protection systems
- Two TSMP should be installed directly next to the master switches protected by a conductive housing that can be opened without tools. TSMPs should be 4mm shrouded banana jacks | EV4.4.1, EV4.4.2 EV4.4.4

Misc.
- A handcart must be provided to transport the accumulators. It must have a dead man's switch i.e. brake is ON by default. | EV8.4.1 EV8.4.2

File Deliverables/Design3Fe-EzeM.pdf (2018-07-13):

Name:; Fe-eze Anyafulu; Project Role:; EV Battery System; Subgroup:; Electric Vehicle; Frontline Task:; EV Team Lead; Design III – Final Design
The Module Busbar will be made of Cu101 grade Copper. It will run along the side of the cells (both +ve and - ve) and connect to them via fusible link wires. The top cylinder will be bent and inserted into the module cap where it will be connected in series with other modules and bolted down with an M10 Nut

Formula Student | CITY RACING 2018 | 1

Programme & Part: Electrical Engineering Part 4

### 1. Mechanical Configuration

Battery Module
The battery module is assembled by taking six Sanyo 20700A cells, Adding an M12 Plastic Spacer and then finally the Cu101 conductor. A fuse wire (see electrical section) is welded in the hole between the battery and conductor. This wire acts as the last line of defence in the case of an overcurrent during charging or the first line in the case of a battery Short Circuit. Six of these cells are connected in parallel and they collectively make one battery module. There are 90 such modules in the entire battery pack (Making a total of 540 cells).

Integrated Module Busbar


Module Cap

Module Side Insert

The Module Cap will be made of ABS Plastic. It has two circular holes at the top where an M10 bolt will be fastened to join the modules in series. There is a side cut to allow insertion of an M10 nut and finally, the rectangular holes at the sides will let the Conductor through from the Module Side Insert

The Module Side insert
(made with ABS) will
accommodate the copper
busbars. The circular spaces are 1mm larger than the
busbar diameter to ensure a nice fit. ABS has a high
tolerance of up to 110C so is adequate for our battery
housing purposes.


Assembling Battery Module

Left: Visualizing Module Assembly Steps Right: Final Module Assembly (Note the M10 Nut inserted into the Module cap)

Each module is in effect an 18.6A (3.1A*6), 3.6Volt battery and 90 modules (18 per section *5sections) will be connected in series to give us a final pack voltage of 324V, I=18.6A (at 1C Discharge, 180A Max. Continuous discharge), P=6.026kW/4.338MJ.

Section Calculations
EV3.3.3 states that each section must be no greater than 120V, 6MJ.
Our section design here is 3.6V*18=64.8V /1.205kWh/ 4.336MJ which meets the requirements.


Battery box assembly


### 2. Electrical Configuration

Battery Management System
Temperature Acquisition Circuit
The temperature sensors will be placed at the end of each cell. The sensor selected is a Texas Instruments LMT-84 in a TO-92 Package. This will be inserted into the module PCB which then connects to a module multiplexer. This multiplexer selects one cell per module and sends the temperature value to the Analog to Digital Converter (ADC), once the temperature is converted and sent to the microcontroller, the microcontroller signals to the multiplexer to take the next cell temperature and this goes on until all six cells in a module are measured. Since there are 18 modules in each section, there will be three such ADCs per section. Each ADC is responsible for six modules. (see block diagrams below) The ADCs send the digital information of the cell temperatures to the Microcontroller using I²C communication. Instead of directly reading all 108 cells in a section (6 cells * 18 modules) which will require 108 analog pins or 18pcs of 8-channel ADCs, we are able to save space and cost by using a local multiplexer to switch temperatures.

The battery box will be made of a 3.2mm thick, 464.2mm*468mm 6061-TS Aluminium plate as a base with four 2.3mm walls (and 200mm high) fastened with M8 bolts to divide the box into five sections and finally four 2.3mm thick external walls (205mm high) fastened with M8 bolts. The internal walls will then be covered with fire retardant formex and 18 modules inserted in each section. The PCB for each section will be inserted in the 32mm gap between the top of the modules and the top of the internal vertical wall.


LMT84 Temperature Sensor and SN74LVxx MUX

The LMT84 is a precision CMOS temperature sensor which has a linear Voltage to temperature behaviour making it superior to NTC sensors (which have nonlinear behaviour and are very much affected by self-heating). It operates between 1.5V to 5V (VDD)

The TI SN74LV4051A-Q1 is an Automotive rated 8 Channel CMOS multiplexer that has one output. The switching is done by the microcontroller and all 90 modules will have their local MUX unit which will all be connected by the same four GPIO pins from the µC. It comes in a compact 8.89*10.63*2.65mm SOIC package and will be inserted in a PCB just above the modules in the battery box. 2V < VDD <5.5V

The TI ADS7828-Q1 is an Automotive rated 12-bit, 8 Channel Analog to Digital Converter (ADC) with an I2C communications port and a 50kHz Sampling rate. It comes in a TSSOP 6.4*5mm package. 2.7V < VDD <5V


Temperature Acquisition Block Diagram (Thick arrows indicate Analog Paths; thin arrows indicate Digital Paths)

Battery Protection
A Renesas ISL92403 IC will be used for battery monitoring, protection and voltage balancing. It has a capacity of 3-8 cells but since our modules are in parallel, each monitor IC will handle 6 modules (i.e. 36 cells) and there will be three per section. It is a semi-autonomous unit that can do all the protection tasks required without the help of a microcontroller(µC), it has I²C communications capability and this will be used by the µC sparingly. This design ensures the micromanagement is done locally and the µC will be for data logging, coulomb counting and last resort interference.

Fuse Wire Rating
We want our fuse wire to melt when current goes over 30A in five seconds


BMS block diagram – Thick red is high voltage, thin red is voltage sense, black and grey are the bidirectional communications channels on the I²C bus (one line for data, and one for the clock), Blue is the Temperature sense (explained above)

Manufacture Plan
3D printing can be used for the rapid prototyping and testing stage. However, because of the cost of 3D printing 90*2=180 side inserts, it is more economical to use injection moulding when the full pack is ready to be produced. The cost of the moulding tool and the will be cheaper than 3D printing all the Plastic parts and if we want to make a standby battery box (to implement the proposed fast change battery feature), the presence of the moulding tool makes it astronomically cheaper the second time around (this shall be explored further in the Cost Report)

The copper busbars will be CNC milled from 2mm thick rectangular Copper bars

Each module will require one PCB running along the side of the ABS side part (to acquire the temperature) and Each section will require one PCB running along the top where the six slave I2C Devices (ADCs and Monitors) will be mounted.

Future work
Testing of design


The circuit will have to be fully simulated and corrections made before the parts are purchased

Stress Testing of Battery Box
The battery box would have to be further analysed using FEA to make sure it can withstand stresses required (40g longitudinal and lateral Acceleration, and 20g vertical acceleration)

Full thermal characteristics to devise cooling system
The cooling systems cannot be devised just yet because the thermal characteristics of the cell are currently unknown. In the new year, a specimen of the cell will be acquired, and an equivalent circuit based on the cell’s thermal behaviour will be made. Then, it will be simulated over racing conditions and the temperature behaviour observed. It is at this point that a cooling system will be picked.


BMS software will have to be written to convert all internal I²C communications to CAN format so that the BMS can interact with the main vehicle ECU over a CAN bus.

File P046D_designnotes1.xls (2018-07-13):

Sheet: Summary
Chief Engineers View 1
Current EV parts Weight | kg |  | Target
Batteries | 32.4 |  | 32.4
Wires etc. | 5.0 |  | 5.0
Motors | 24.9 |  | 24.9
Esc | 2.6 |  | 2.6
Front Suspension | 30.6 |  | 26.0
Rear Suspension | 29.5 |  | 27.0
Steering | 5.4 |  | 5.4
Monocoque | 10.0 |  | 10.0
10" Wheels | 22.0 |  | 22.0
Misc | 52.0 |  | 20.0
Total | 214.4 |  | 175.3
Cost
 | Option 1 |  | 50 | 150 | 300
Batteries | £1944 |  | £1944 | £1944 | £1944
Spare Batteries
Motors | £2990 |  | £2990 | £2990 | £2990
Esc | £500 |  | £500 | £500 | £500
battery accoutrements | £1704 |  | £198.7 | £114.22 | £75.16
TxRx | £180 |  | £180 | £180 | £180
Chargers | £2000 |  | £2000 | £2000 | £2000
body etc | £9222 |  | £9000 | £8500 | £8000
Total | 18540.00 |  | 16812.70 | 16228.22 | 15689.16
 |  |  | £19999 | £18999 | £18499 | 4people
 |  | fake profit | 159315 | 415617 | 842952
 |  | salary | 120000 | 120000 | 120000
 |  | rent/electricity | 12000 | 12000 | 12000
 |  | net profit | 27315 | 283617 | 710952
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

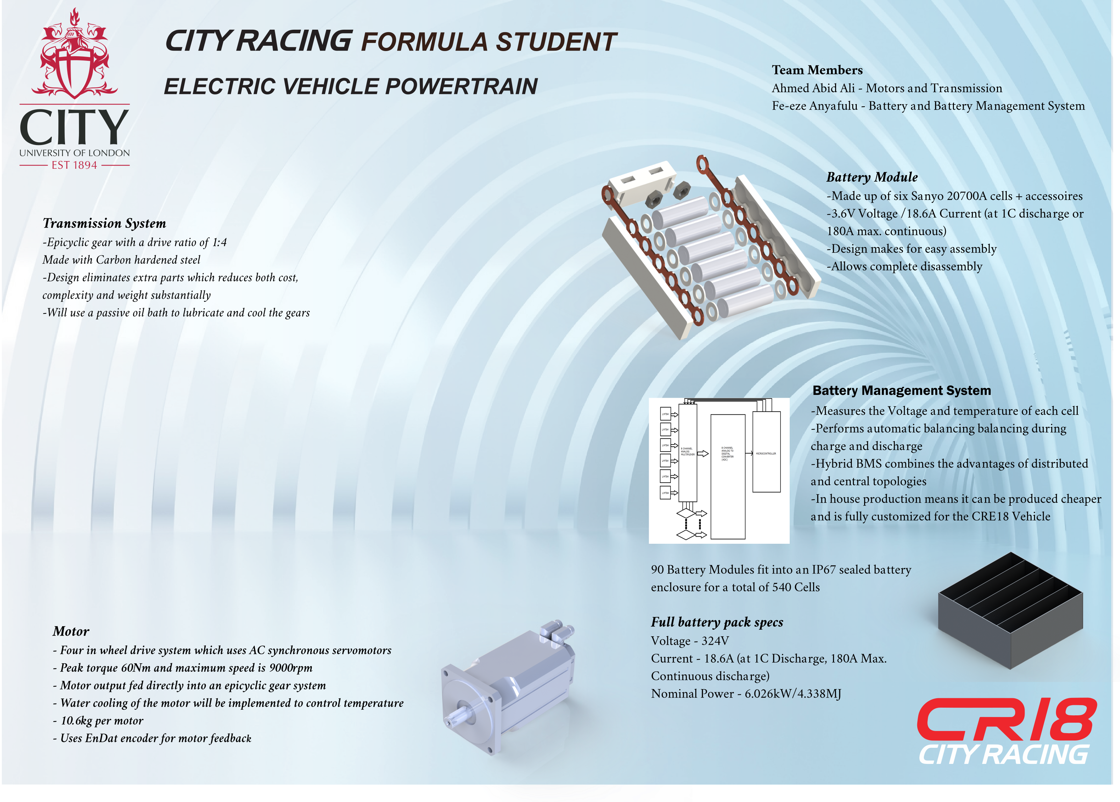
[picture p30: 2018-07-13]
Deliverables/Poster.png

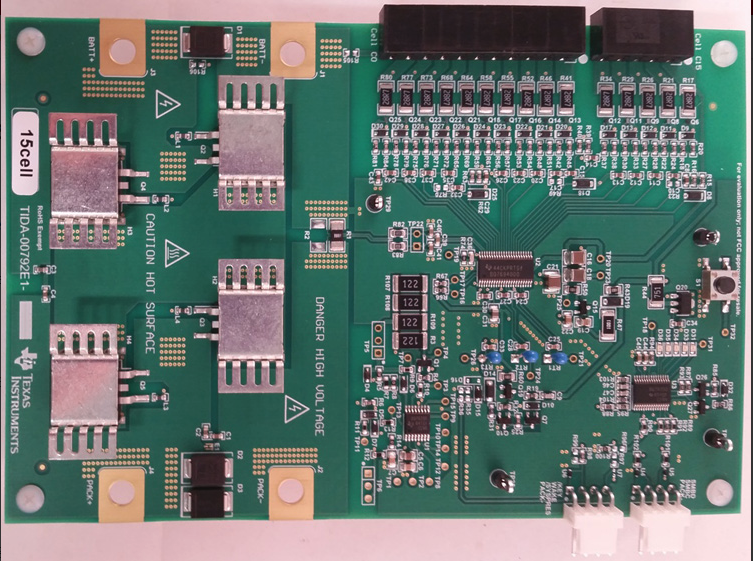
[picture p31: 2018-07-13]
Deliverables/imgs/bms.PNG

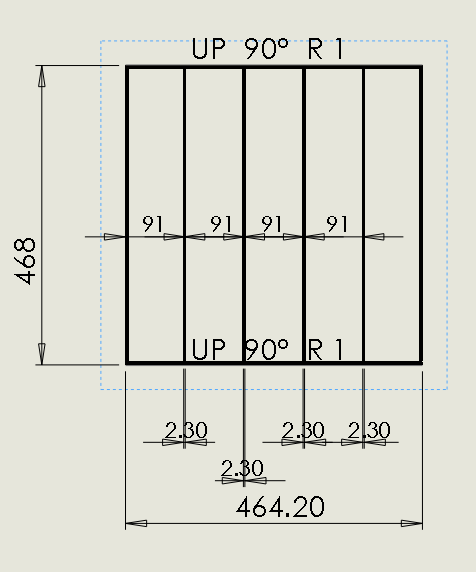
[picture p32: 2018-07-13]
Deliverables/sheetmetalbox.PNG

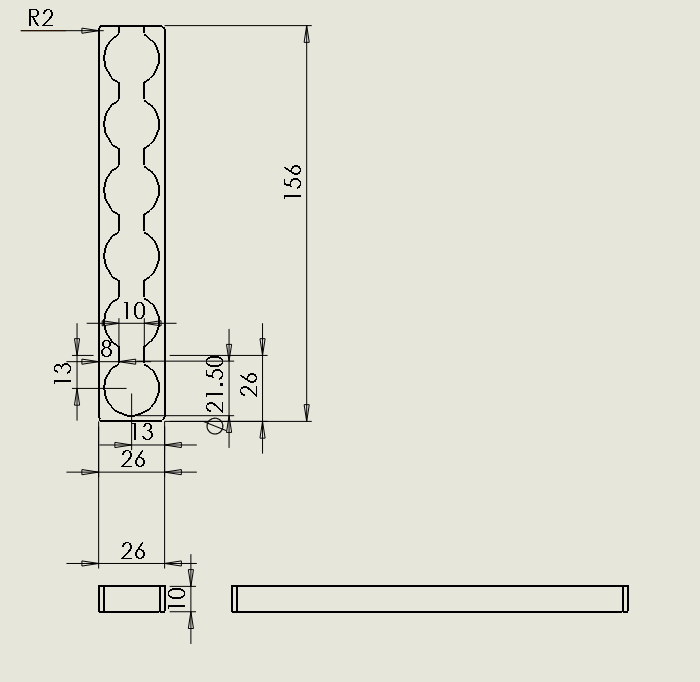
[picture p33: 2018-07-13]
Deliverables/BatterySideDrawing.PNG

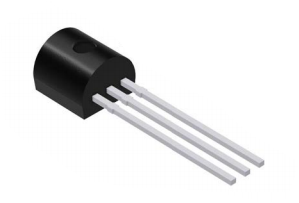
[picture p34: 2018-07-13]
Deliverables/TO92.PNG

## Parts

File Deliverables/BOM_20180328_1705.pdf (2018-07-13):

## Car No University Team Name

### Formula Student 2018: 11-15 July 2018

### Cover photo - Car Photo Insert>Picture

€ 0.00

System Assembly | Part | M/B P/M/F/T | Comments | Qt | Cost (per piece)
Cost Comments | ID
BRAKES | Total | 1 | € 0.00 | € 0.00
ENGINE & DRIVETRAIN | Total | 1 | € 0.00 | € 0.00
FRAME & BODY | Total | 1 | € 0.00 | € 0.00
ELECTRICAL | Total | 1 | € 0.00 | € 0.00
EL | HV-Battery | 1 | EL-A-0400
LG HB2 18650 Cell | b | 1125 | EL-400-010
Battery Box | m | 1 | EL-400-011
M | Aluminum | 4mm thick Al sheet | 1 | EL-400-011-01
P | Plasma Cutting | Cut out the two sides from Sheet metal 2 | EL-400-011-02
P | Plasma Cutting | Cut out the base | 1 | EL-400-011-04
P | Plasma Cutting | Cut out the back piece | 1 | EL-400-011-05
P | Plasma Cutting | Cut out the inner dividers | 5 | EL-400-011-06
P | Plasma Cutting | Cut out the front divider piece | 1 | EL-400-011-07
P | Plasma Cutting | Cut out the front piece | 1 | EL-400-011-08
P | Plasma Cutting | Cut out the top cover | 1 | EL-400-011-09
P | Adjustment - Misc. | Bend Pieces to create flanges as needed 11 | EL-400-011-010
MISCELLANEOUS, FIT, FINISH & ASSEMBLY | Total | 1 | € 0.00 | € 0.00
STEERING SYSTEM | Total | 1 | € 0.00 | € 0.00
SUSPENSION SYSTEM | Total | 1 | € 0.00 | € 0.00
WHEELS, WHEEL BEARINGS AND TIRES | Total | 1 | € 0.00 | € 0.00
DRIVERLESS | Total | 1 | € 0.00

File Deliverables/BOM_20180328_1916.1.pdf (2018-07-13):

€ 0.00

System Assembly | Part | M/B P/M/F/T | Comments | Qt | Cost (per piece)
Cost Comments | ID
BRAKES | Total | 1 | € 0.00 | € 0.00
ENGINE & DRIVETRAIN | Total | 1 | € 0.00 | € 0.00
FRAME & BODY | Total | 1 | € 0.00 | € 0.00
ELECTRICAL | Total | 1 | € 0.00 | € 0.00
EL | HV-Battery | 1 | EL-A-0400
LG HB2 18650 Cell | b | 1125 | EL-400-010
Battery Box | m | 1 | EL-400-011
M | Aluminum | 4mm thick Al sheet | 1 | EL-400-011-01
P | Plasma Cutting | Cut out the two sides from Sheet metal 2 | EL-400-011-02
P | Plasma Cutting | Cut out the base | 1 | EL-400-011-04
P | Plasma Cutting | Cut out the back piece | 1 | EL-400-011-05
P | Plasma Cutting | Cut out the inner dividers | 5 | EL-400-011-06
P | Plasma Cutting | Cut out the front divider piece | 1 | EL-400-011-07
P | Plasma Cutting | Cut out the front piece | 1 | EL-400-011-08
P | Plasma Cutting | Cut out the top cover | 1 | EL-400-011-09
P | Adjustment - Misc. | Bend Pieces to create flanges as needed 11 | EL-400-011-010
P | Drilled hole | Drill holes in Front Divider Piece and back piece to hold maintainance plugs 8 | EL-400-011-027
P | Drilled hole | Make holes for fasteners | 132 | EL-400-011-011
F | Rivet | 132 | EL-400-011-016
P | Riveting | Use rivets to fasten pieces | 132 | EL-400-011-017
M | Rubber | Rubber Sealing Gasket | 1 | EL-400-011-018
P | Cut (scissors, knife) | Cut gasket to size of exposed flanges1 | EL-400-011-019
P | Resin Application | Glue Gasket to Top cover | 1 | EL-400-011-020
P | Drilled hole | Make holes in Top Cover, Front Flange, Side flanges and Back flange for fastener 24 | EL-400-011-021
F | Bolt | For sealing top cover to box | 24 | EL-400-011-022
F | Nut | For sealing Top Cover to box | 24 | EL-400-011-023
P | Cut (scissors, knife) | Cut Nomex Paper to inner dimensions 1 | EL-400-011-025
P | Resin Application | Glue Nomex to the inside of the assembled box 1 | EL-400-011-026
P | Assemble | Insert completed sections into Box 5 | EL-400-011-052
Copper Busbars | m | Made from Cu101 (Electrical grade Copper) sheet 150 | EL-400-012
M | Copper | 2mm sheet | 1 | EL-400-012-028
P | Plasma Cutting | Cut into copper busbars | 150 | EL-400-012-029
Parallel String | m | 75 | EL-400-016
M | Electronic Component | LG HB2 | 15 | EL-400-016-042
M | Plastic | 18650 Cell Spacers | 30 | EL-400-016-043
M | Copper | Copper Busbars | 2 | EL-400-016-044

M | Electronic Component | Temperature Circuit | 1 | EL-400-016-045
P | Assemble | Clip Cells to spacers | 30 | EL-400-016-046
P | Weld | Spot Weld Copper Busbars to cell tabs 2 | EL-400-016-047
P | Resin Application | Glue temprerature sensors from Temp PCB to negative busbar 1 | EL-400-016-048
P | Fastener Install (every) Screw in PCB to end of cell spacers2 | EL-400-016-049
Battery Section | m | aka Brick | 5 | | EL-400-017
M | Electronic Component | Parallel String | 15 | EL-400-017-050
M | Electronic Component | Section PCB | 1 | EL-400-017-051
P | Assemble | Join 15 Parallel strings to form a section 15 | EL-400-017-053
P | Wire Dressing (Install and Route) Install wires to connect Temp PCB to section PCB 15 | EL-400-017-054
P | Weld | Connect busbars (from parallel strings) in series 15 | EL-400-017-055
P | Wire Dressing (Install and Route) Install Voltage taps on series connections and connect other end to section pcb 15 | EL-400-017-056
F | Crimp Terminal | M10 Uninsulated terminal | 1 | EL-400-017-057
F | Nut | M10 locknut | 2 | EL-400-017-058
F | Washer | M10 | 2 | EL-400-017-059
F | Screw | M10 | 1 | EL-400-017-060
M | Plastic | Anderson Powerpole PP180 Housing1 | EL-400-017-061
M | Copper | Anderson Powerpole Contact | 1 | EL-400-017-062
P | Assemble | Assemble Maintainance plug | 1 | EL-400-017-063
P | Fastener Install (every) Screw maintainance plugs into back wall 1 | EL-400-017-064
Battery Charger | b | Emotorwerks 40A/10kWh | 1 | € 580.00 | EL-400-018
000AWG wire | b | | 1 | | EL-400-019
Shutdown Switches | b | XB4 Pushbutton switch | 3 | | EL-400-020
XB4 Collar | b | | 3 | | EL-400-021
XB4 Legend Plate | b | | 3 | | EL-400-022
Main Fuse | b | Littelfuse Class L, LDC series 600V/450A fuse 1 | EL-400-023
Accumulator Insulator Relay b | TE Kilovac EV200 | 2 | EL-400-024
Insulation Monitoring Device b | Bender Isometer IR155-3204 | 1 | EL-400-025
Inertia Switch | b | Pegasus Racing Inertia Switch | 1 | | EL-400-026
High Voltage Disconnect b | Anderson SBX Series 2 Way Male/Female 1 | EL-400-027
HVD handle | b | Frame Handle, For Use With SB series connectors 1 | EL-400-028
Master Switches | b | 0-605-21 75A Rated at 24V Battery Isolator with Removable Key in Off Position 2 | EL-400-029
Tractive System Measuring Points b | Cinch Connectors Red Banana Jack, 15A, 3.5kV, Tin Plated 1 | EL-400-030
EL | Battery Management System | BMS | 1 | EL-A-0404
Section PCB | m | 5 | EL-404-014
M | Electronic Component | BQ76940, Batter Monitor and Protection Analog Front End 1 | EL-404-014-034
M | Electronic Component | BQ78350-r1m CEDV Li-ion Guage IC1 | EL-404-014-035
M | Electronic Component | FET Driver, BQ76200 | 1 | EL-404-014-036
M | Electronic Component | Blank PCB | 1 | EL-404-014-037
M | Electronic Component | Capacitor, 0.22 microfarads, 0603 19 | EL-404-014-073
M | Electronic Component | Capacitor, 1.5 microfarads, 0805 | 1 | EL-404-014-074
M | Electronic Component | Capacitor, 0.1 microfarads, 0603 | 4 | EL-404-014-075
M | Electronic Component | Capacitor, 470picofarads, 0603 | 2 | EL-404-014-076

M | Electronic Component | Capacitor, 0.1 microfarads, 0603 | 5 | EL-404-014-077
M | Electronic Component | Capacitor, 10 microfarad, 1210 | 3 | EL-404-014-078
M | Electronic Component | MOSFET, N/P-CH, 12V, 2.1A | 15 | EL-404-014-079
M | Electronic Component | Diode, Ultrafast, 100V, SOD-123 | 5 | EL-404-014-080
M | Electronic Component | Resistor, 100 Ohm, 0805 | 2 | EL-404-014-081
M | Electronic Component | Resistor, 100 kiloohm, 0805 | 3 | EL-404-014-082
M | Electronic Component | Resistor, 300kiloOhm, 0603 | 4 | EL-404-014-083
P | Assemble | Solder Electronic Components to Board 1 | EL-404-014-084
Temperature Acquisition Circuit m | 75 | EL-404-015
M | Electronic Component | Blank PCB | 1 | EL-404-015-038
M | Electronic Component | Resistor, 20 0hm | 1 | EL-404-015-039
M | Electronic Component | Capacitor, 10 Microfarad | 1 | EL-404-015-040
M | Electronic Component | Inductor, 10 MicroHenry | 1 | EL-404-015-041
M | Electronic Component | Resistor, 385 KiloOhms | 1 | EL-404-015-065
M | Electronic Component | Resistor, 125 KiloOhms | 1 | EL-404-015-066
M | Plastic | Header, Female, 1row 3 pin | 8 | EL-404-015-067
M | Electronic Component | SN74LV4051A, 8 Channel Analog Multiplexer 1 | EL-404-015-068
M | Electronic Component | LM3670 DC-DC buck converter | 1 | EL-404-015-069
M | Electronic Component | LMT84, 3-Pin Thermometer, TO92 Package 8 | EL-404-015-070
M | Plastic | Header, JXT-SH, Male, 7 pin | 1 | EL-404-015-071
P | Assemble | Solder Electronic Components to Fabricated PCB 1 | EL-404-015-072
MSP430 Ultra-Low Power Microcontroller b | Main MCU | 1 | EL-404-031
MISCELLANEOUS, FIT, FINISH & ASSEMBLY | Total | 1 | € 0.00 | € 0.00
STEERING SYSTEM | Total | 1 | € 0.00 | € 0.00
SUSPENSION SYSTEM | Total | 1 | € 0.00 | € 0.00
WHEELS, WHEEL BEARINGS AND TIRES | Total | 1 | € 0.00 | € 0.00
DRIVERLESS | Total | 1 | € 0.00

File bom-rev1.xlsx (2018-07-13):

Generated Date | Fri 09 Feb 2018 14:36:55 GMT
Title | BOM for Battery Assembly (first draft)
Company | CRE18
Revision | 1
Date Issue | 2018-02-08
Reference | Part | Value | Manufacturer | Supplier | Number needed | x amount to be bought | Price | Purchase Link
Battery Module | Battery Module Side Insert 1 | PBM18E003A | self |  | 90 |  | 0 | This is the approx cost for 3d printing; Injection moulding is much more expensive because we are not mass manufacturing. Quote for CNC milling pending. Need to go back to the drawing board to simplify part; make both parts identical
Battery Module | Battery Module Side Insert 2 | PBM18E002A | self |  | 90 |  | 0
Battery Module | Battery Busbar made from 2mm Cu-101 sheet | PBM18E004A | self |  | sheet
Battery Module | LG HB2 18650 Cell | PBM18E001A | LG |  | 1000 | 750 | 2000 | pending response from supplier
Battery Module | M12 Nylon Plastic Washer | M12 |  |  | 540
Battery Module | Fuse Wire |  |  |  | 540
Battery Module | M12*20 Hex nut | M12*20 |  |  | 180 | 20
Battery Section | Insulated terminal ring crimp connectors |  |  |  | 100
Battery Section | 10AWG wire | 10AWG
Battery Section | UL-94V1 flame resistant paper |  | Molex
Battery Box | Aluminium Sheet Metal for battery enclosure
Temperature Acquisition circuit (Battery Module) | 20 Ohm resistor | 20 | Vishay/Murata | Mouser | 90
Temperature Acquisition circuit (Battery Module) | 10 microfarad capacitor | 10u | Vishay/Murata | Mouser | 90
Temperature Acquisition circuit (Battery Module) | 10 microhenry inductor | 10u | Vishay/Murata | Mouser | 90
Temperature Acquisition circuit (Battery Module) | 4.7 microfarad capacitor | 4.7u | Vishay/Murata | Mouser | 90
Temperature Acquisition circuit (Battery Module) | 125 kiloohm resistor | 125k | Vishay/Murata | Mouser | 90
Temperature Acquisition circuit (Battery Module) | 385 kiloohm resistor | 385k | Vishay/Murata | Mouser | 90 | 100 | 10.9 | https://www.mouser.co.uk/ProductDetail/Vishay-Dale/RN55D4003FB14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
Temperature Acquisition circuit (Battery Module) | female 1row 3 pin straight pin header | CONN_01X03_FEMALE |  |  | 720 | for all headers | 10 | https://www.aliexpress.com/item/Free-Shipping-10PCS-40pin-2-54mm-pitch-single-row-11mm-row-female-connectors/1929060681.html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
Temperature Acquisition circuit (Battery Module) | 8 Channel analog multiplexer | SN74LV4051A | Texas Instruments | Digikey | 90 | 100 | 19.9 | https://www.mouser.co.uk/ProductDetail/Texas-Instruments/SN74LV4051AQPWRQ1
Temperature Acquisition circuit (Battery Module) | DC-DC buck converter | LM3670 | Texas Instruments | Digikey | 90 | 100 | 50.5 | https://www.mouser.co.uk/ProductDetail/Texas-Instruments/LM3670MF-ADJ-NOPB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
Temperature Acquisition circuit (Battery Module) | Male 1 row 5 pin straight pin header | CONN_01X05 |  |  | 90
Temperature Acquisition circuit (Battery Module) | female 1row 2 pin straight pin header | CONN_01X02_FEMALE |  |  | 90
Temperature Acquisition circuit (Battery Module) | 3 pin TO-92 package thermometer | LMT84 | Texas Instruments | Digikey | 720 | 800 | 240 | https://www.mouser.co.uk/ProductDetail/595-LMT84LPM
Temperature Acquisition circuit (Battery Module) | Module PCB | PCB1 | self | Seeed Studio | 90 | 100 | 37.95 | https://www.seeedstudio.com/fusion_pcb.html
BMS Section Monitoring Circuit | Analog Front End BMS section protection IC | BQ76940 | Texas Instruments | Digikey | 6 | 10 | 50.3 | https://www.mouser.co.uk/ProductDetail/Texas-Instruments/BQ7694001DBT
BMS Section Monitoring Circuit | CEDV Li-ion Gas guage | BQ78350-r1 | Texas Instruments | Digikey | 6 | 10 | 31.1 | https://www.mouser.co.uk/ProductDetail/Texas-Instruments/BQ78350DBTR-R1
BMS Section Monitoring Circuit | High Voltage Front End charge/discharge high side NFET | BQ76200 | Texas Instruments | Digikey | 6 | 10 | 16.2 | https://www.mouser.co.uk/ProductDetail/Texas-Instruments/BQ76200PWR
BMS Section Monitoring Circuit | Section PCB | PCB2 | self | Seeed Studio | 6 | 10 | 33
BMS Main board | Main circuit Microcontroller (16 bit, Ultra low power) | MSP430F5528 | Texas Instruments | Digikey | 1 | 2 | 10.36 | https://www.mouser.co.uk/ProductDetail/Texas-Instruments/MSP430F5528IRGCR
BMS Main board | Main board PCB | PCB3 | self | Seeed Studio | 1 | 1 | 10
 | Battery Charger |  |  |  |  |  | 400
 | Battery Spot welding | 50p per cell |  |  | 720 | 720 | 360
Drivetrain | Servomotors |  | TGN Drives |  | 4 | 4 | 2856
Drivetrain | Motor Driver |  |  |  | 4 | 4 | 2000
Drivetrain | Epicyclic Gear |  |  |  | 4 | 4 | 340
 |  |  |  |  |  |  | 8476.21 | we shall cut costs in the plastic part to make this more feasible

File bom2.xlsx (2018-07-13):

# needed | part |  |  | price
14 | te lug | https://uk.rs-online.com/web/p/crimp-ring-terminals/7455961/
14 | m10 locknut | https://www.accu.co.uk/en/hexagon-nylon-locking-nuts/7950-HNN-M10-A2
14 | m10 washer | https://www.accu.co.uk/en/flat-washers/72471-HPW-M10-A2
14 | m10 screw | https://www.accu.co.uk/en/socket-button-screws/8221-SSB-M10-25-A2
 | datasheet | https://www.andersonpower.com/_global-assets/downloads/pdf/ds-pp180.pdf
 | page | https://www.andersonpower.com/us/en/products/powerpole/index.aspx
7 | red anderson | http://uk.farnell.com/anderson-power-products/1381g3/plug-rcpt-housing-1pos-red/dp/2576120
7 | black | http://uk.farnell.com/anderson-power-products/1381g1/plugsocket-connector-housing/dp/7618591?ost=1381g1
14 | contacts
 | 000 awg wire | https://www.altecautomotive.co.uk/95mm2-000-awg-automotive-batterystarter-cable-50000-amps-5034-p.asp
 | lv wire | https://www.altecautomotive.co.uk/05mm-sq-20-awg-auto-cable--11-amp-rating-50mtrs-br-alttw05-01-257-p.asp
3 | xb4 shutdown switches | https://uk.rs-online.com/web/p/emergency-stop-push-buttons/7951306/ | https://docs-emea.rs-online.com/webdocs/13dc/0900766b813dce93.pdf | #26.87
 | xb4 collar | https://uk.rs-online.com/web/p/push-button-accessories/3310142/
 | xb4 legend plate | https://uk.rs-online.com/web/p/push-button-accessories/8827897/
 | littelfuse main fuse | http://www.littelfuse.com/products/fuses/industrial-power-fuses/class-l-fuses.aspx
2 | air | http://www.te.com/commerce/DocumentDelivery/DDEController?Action=showdoc
2 | air option 2 | http://www.te.com/commerce/DocumentDelivery/DDEController?Action=showdoc
 | imd | http://www.bender-es.com/en/products/c/insulation_monitoring__1/special_applications__4/isometerr_ir155-3203_ir155-3204__343.html |  | 150 us; anectodtal; email sent; awaiting response
 | inertia switch | https://www.pegasusautoracing.com/productdetails.asp?RecID=87 |  | 60 us
 | inertia switch | https://shop.advanceautoparts.com/p/wells-vehicle-electronics-fuel-pump-inertia-switch-sw4177/10288584-P |  | 99 us
 | charger | https://emotorwerks.com/store/residential/juicebox-pro-40-smart-40-amp-evse-with-24-foot-cable |  | 580 usd
 | bots | https://uk.rs-online.com/web/p/toggle-switches/4175451/ | single pole single throw switch
 | tsmps | https://uk.rs-online.com/web/p/2-mm-test-plugs-sockets/8860917/
 | hvd interlock | https://uk.rs-online.com/web/p/heavy-duty-power-connector-kits/6120144/ | http://www.andersonpower.com/us/en/products/sbe-sbx-sbo/sbe-320-and-sbx-350.aspx | 24.06
 | frame handle for hvd | https://uk.rs-online.com/web/p/heavy-duty-power-connector-accessories/7153546/ | https://uk.rs-online.com/web/p/heavy-duty-power-connector-accessories/7153555/ | 13.07 | 13.63
2 | master switches | https://www.arc-components.com/0-605-21-75a-rated-at-24v-battery-isolator-with-removable-key-in-off-position-2327.html | https://uk.rs-online.com/web/p/key-switches/3254856/ | 44.51 | 51.58
 | TSAL | https://uk.rs-online.com/web/p/beacons/9075959/ |  | 51.6
 | speaker for rtds | https://uk.rs-online.com/web/p/piezoelectric-miniature-speakers/2945668/?searchTerm=100db+speaker |  | 4.93

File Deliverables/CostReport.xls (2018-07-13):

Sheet: EnclosedCell
University | City University of London |  |  |  |  |  |  |  | Car # | 11 |  | Asm Cost | #DIV/0!
System | Battery |  |  |  |  |  |  |  |  |  |  | Qty | 900
Assembly | Cell |  |  |  |  |  |  |  | FileLink1
P/N Base | A3421 |  |  |  |  |  |  |  | FileLink2 |  |  | Extended Cost | #DIV/0!
Suffix | AA |  |  |  |  |  |  |  | FileLink3
Details | Preparing the cell for installation
ItemOrder | Part | Part Cost | Quantity | Sub Total
1 | LG HB2 Cell | $1.90 | 1 | $1.900
2 | ABS 18650 holder | $0.50 | 2 | $1.000
 |  |  |  | $0.000
 |  |  |  | $0.000
 |  |  | Sub Total | $2.900
ItemOrder | Material | Use | UnitCost | Size1 | Unit1 | Size2 | Unit2 | Area Name | Area | Length | Density | Quantity | Sub Total
1 | Nickel strip | For soldering | $2.00 | 20 | mm | 40 | mm |  |  |  |  | 2.00 | $4.00 | change dims
 |  |  |  |  |  |  |  |  |  |  |  |  | $0.00
 |  |  |  |  |  |  |  |  |  |  |  | Sub Total | $4.000
ItemOrder | Process | Use | UnitCost | Unit | Quantity | Multiplier | Mult. Val. | Sub Total
 | Spot weld Nickel tabs to cell terminals | To avoid soldering directly onto cell terminals | $0.55 |  | 1 | 1 | 1 | $0.55
 | Insert Cell into holder |  |  |  |  |  |  | $0.00
 |  |  |  |  |  |  |  | $0.00
 |  |  |  |  |  |  |  | Sub Total | 0.55
ItemOrder | Fastener | Use | UnitCost | Size1 | Unit1 | Size2 | Unit2 | Quantity | Sub Total
 |  |  |  |  |  |  |  | Sub Total | $0.00
ItemOrder | Tooling | Use | UnitCost | Unit | Quantity | PVF | FractionIncluded | Sub Total
 |  |  |  |  |  |  |  | #DIV/0!
 |  |  |  |  |  |  |  | #DIV/0!
 |  |  |  |  |  |  | Sub Total | #DIV/0!

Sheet: ModuleCopperBusbar
University | City, University of London |  |  |  |  |  |  |  | Car # | 11 |  | Part Cost | $20.24
System | Battery |  | FileLink1 |  |  |  |  |  |  |  |  | Qty | 180
Assembly | Module Assembly |  | FileLink2 |  |  |  |  |  | FileLink1
Part | Copper Busbar |  | FileLink3 |  |  |  |  |  | FileLink2 |  |  | Extended Cost | $3642.94
P/N Base |  |  |  |  |  |  |  |  | FileLink3
Suffix | AA
Details | Creating copper
ItemOrder | Material | Use | UnitCost | Size1 | Unit1 | Size2 | Unit2 | Area Name | Area | Length | Density | Quantity | Sub Total
 | Cu-101 | Busbar |  |  |  |  |  |  |  |  |  |  | $0.00 | copper sheet size?
 |  |  |  |  |  |  |  |  |  |  |  |  | $0.00
30 | Bearing | Rocker bearing | $10.12 | 20 | mm | 40 | mm |  |  |  |  | 2.00 | $20.24
 |  |  |  |  |  |  |  |  |  |  |  |  | $0.00
 |  |  |  |  |  |  |  |  |  |  |  |  | $0.00
 |  |  |  |  |  |  |  |  |  |  |  |  | $0.00
 |  |  |  |  |  |  |  |  |  |  |  |  | $0.00
 |  |  |  |  |  |  |  |  |  |  |  |  | $0.00
 |  |  |  |  |  |  |  |  |  |  |  | Sub Total | $20.239
ItemOrder | Process | Use | UnitCost | Unit | Quantity | Multiplier | Mult. Val. | Sub Total
 |  |  |  |  |  |  |  | $0.00
 |  |  |  |  |  |  |  | $0.00
 |  |  |  |  |  |  |  | $0.00
 |  |  |  |  |  |  |  | $0.00
 |  |  |  |  |  |  |  | $0.00
 |  |  |  |  |  |  |  | $0.00
 |  |  |  |  |  |  |  | $0.00
 |  |  |  |  |  |  |  | $0.00
 |  |  |  |  |  |  | Sub Total | $0.00
ItemOrder | Fastener | Use | UnitCost | Size1 | Unit1 | Size2 | Unit2 | Quantity | Sub Total
 |  |  |  |  |  |  |  |  | $0.00
 |  |  |  |  |  |  |  |  | $0.00
 |  |  |  |  |  |  |  |  | $0.00
 |  |  |  |  |  |  |  |  | $0.00
 |  |  |  |  |  |  |  |  | $0.00
 |  |  |  |  |  |  |  |  | $0.00
 |  |  |  |  |  |  |  |  | $0.00
 |  |  |  |  |  |  |  |  | $0.00
 |  |  |  |  |  |  |  | Sub Total | $0.00
ItemOrder | Tooling | Use | UnitCost | Unit | Quantity | PVF | FracIncld | Sub Total
 |  |  |  |  |  |  | Sub Total | 0
#REF! | #REF! | #REF! | #REF! | #REF! | #REF! | #REF! | #REF!
#REF! | #REF! | #REF! | #REF! | #REF! | #REF! | #REF! | #REF!
#REF! | #REF! | #REF! | #REF! | #REF! | #REF! | #REF! | #REF!
#REF! | #REF! | #REF! | #REF! | #REF! | #REF! | #REF! | #REF!
#REF! | #REF! | #REF! | #REF! | #REF! | #REF! | #REF! | #REF!
#REF! | #REF! | #REF! | #REF! | #REF! | #REF! | #REF! | #REF!
#REF! | #REF! | #REF! | #REF! | #REF! | #REF! | #REF! | #REF!
#REF! | #REF! | #REF! | #REF! | #REF! | #REF! | #REF! | #REF!
#REF! | #REF! | #REF! | #REF! | #REF! | #REF! | #REF! | #REF!
#REF! | #REF! | #REF! | #REF! | #REF! | #REF! | #REF! | #REF!
#REF! | #REF! | #REF! | #REF! | #REF! | #REF! | #REF! | #REF!
#REF! | #REF! | #REF! | #REF! | #REF! | #REF! | #REF! | #REF!
#REF! | #REF! | #REF! | #REF! | #REF! | #REF! | #REF! | #REF!
#REF! | #REF! | #REF! | #REF! | #REF! | #REF! | #REF! | #REF!
#REF! | #REF! | #REF! | #REF! | #REF! | #REF! | #REF! | #REF!
#REF! | #REF! | #REF! | #REF! | #REF! | #REF! | #REF! | #REF!
#REF! | #REF! | #REF! | #REF! | #REF! | #REF! | #REF! | #REF!
#REF! | #REF! | #REF! | #REF! | #REF! | #REF! | #REF! | #REF!
#REF! | #REF! | #REF! | #REF! | #REF! | #REF! | #REF! | #REF!
#REF! | #REF! | #REF! | #REF! | #REF! | #REF! | #REF! | #REF!
#REF! | #REF! | #REF! | #REF! | #REF! | #REF! | #REF! | #REF!
#REF! | #REF! | #REF! | #REF! | #REF! | #REF! | #REF! | #REF!
#REF! | #REF! | #REF! | #REF! | #REF! | #REF! | #REF! | #REF!
#REF! | #REF! | #REF! | #REF! | #REF! | #REF! | #REF! | #REF!
#REF! | #REF! | #REF! | #REF! | #REF! | #REF! | #REF! | #REF!
#REF! | #REF! | #REF! | #REF! | #REF! | #REF! | #REF! | #REF!
#REF! | #REF! | #REF! | #REF! | #REF! | #REF! | #REF! | #REF!
#REF! | #REF! | #REF! | #REF! | #REF! | #REF! | #REF! | #REF!
#REF! | #REF! | #REF! | #REF! | #REF! | #REF! | #REF! | #REF!
#REF! | #REF! | #REF! | #REF! | #REF! | #REF! | #REF! | #REF!
#REF! | #REF! | #REF! | #REF! | #REF! | #REF! | #REF! | #REF!
#REF! | #REF! | #REF! | #REF! | #REF! | #REF! | #REF! | #REF!
#REF! | #REF! | #REF! | #REF! | #REF! | #REF! | #REF! | #REF!
#REF! | #REF! | #REF! | #REF! | #REF! | #REF! | #REF! | #REF!
#REF! | #REF! | #REF! | #REF! | #REF! | #REF! | #REF! | #REF!
#REF! | #REF! | #REF! | #REF! | #REF! | #REF! | #REF! | #REF!
#REF! | #REF! | #REF! | #REF! | #REF! | #REF! | #REF! | #REF!
#REF! | #REF! | #REF! | #REF! | #REF! | #REF! | #REF! | #REF!
#REF! | #REF! | #REF! | #REF! | #REF! | #REF! | #REF! | #REF!
#REF! | #REF! | #REF! | #REF! | #REF! | #REF! | #REF! | #REF!
#REF! | #REF! | #REF! | #REF! | #REF! | #REF! | #REF! | #REF!
#REF! | #REF! | #REF! | #REF! | #REF! | #REF! | #REF! | #REF!
#REF! | #REF! | #REF! | #REF! | #REF! | #REF! | #REF! | #REF!
#REF! | #REF! | #REF! | #REF! | #REF! | #REF! | #REF! | #REF!
#REF! | #REF! | #REF! | #REF! | #REF! | #REF! | #REF! | #REF!
#REF! | #REF! | #REF! | #REF! | #REF! | #REF! | #REF! | #REF!
#REF! | #REF! | #REF! | #REF! | #REF! | #REF! | #REF! | #REF!
#REF! | #REF! | #REF! | #REF! | #REF! | #REF! | #REF! | #REF!
#REF! | #REF! | #REF! | #REF! | #REF! | #REF! | #REF! | #REF!
#REF! | #REF! | #REF! | #REF! | #REF! | #REF! | #REF! | #REF!
#REF! | #REF! | #REF! | #REF! | #REF! | #REF! | #REF! | #REF!
#REF! | #REF! | #REF! | #REF! | #REF! | #REF! | #REF! | #REF!
#REF! | #REF! | #REF! | #REF! | #REF! | #REF! | #REF! | #REF!
#REF! | #REF! | #REF! | #REF! | #REF! | #REF! | #REF! | #REF!
#REF! | #REF! | #REF! | #REF! | #REF! | #REF! | #REF! | #REF!
#REF! | #REF! | #REF! | #REF! | #REF! | #REF! | #REF! | #REF!
#REF! | #REF! | #REF! | #REF! | #REF! | #REF! | #REF! | #REF!
#REF! | #REF! | #REF! | #REF! | #REF! | #REF! | #REF! | #REF!
#REF! | #REF! | #REF! | #REF! | #REF! | #REF! | #REF! | #REF!
#REF! | #REF! | #REF! | #REF! | #REF! | #REF! | #REF! | #REF!
#REF! | #REF! | #REF! | #REF! | #REF! | #REF! | #REF! | #REF!
#REF! | #REF! | #REF! | #REF! | #REF! | #REF! | #REF! | #REF!
#REF! | #REF! | #REF! | #REF! | #REF! | #REF! | #REF! | #REF!
#REF! | #REF! | #REF! | #REF! | #REF! | #REF! | #REF! | #REF!
#REF! | #REF! | #REF! | #REF! | #REF! | #REF! | #REF! | #REF!
#REF! | #REF! | #REF! | #REF! | #REF! | #REF! | #REF! | #REF!
#REF! | #REF! | #REF! | #REF! | #REF! | #REF! | #REF! | #REF!
#REF! | #REF! | #REF! | #REF! | #REF! | #REF! | #REF! | #REF!
#REF! | #REF! | #REF! | #REF! | #REF! | #REF! | #REF! | #REF!
#REF! | #REF! | #REF! | #REF! | #REF! | #REF! | #REF! | #REF!
#REF! | #REF! | #REF! | #REF! | #REF! | #REF! | #REF! | #REF!
#REF! | #REF! | #REF! | #REF! | #REF! | #REF! | #REF! | #REF!
#REF! | #REF! | #REF! | #REF! | #REF! | #REF! | #REF! | #REF!
#REF! | #REF! | #REF! | #REF! | #REF! | #REF! | #REF! | #REF!
#REF! | #REF! | #REF! | #REF! | #REF! | #REF! | #REF! | #REF!
#REF! | #REF! | #REF! | #REF! | #REF! | #REF! | #REF! | #REF!
#REF! | #REF! | #REF! | #REF! | #REF! | #REF! | #REF! | #REF!
#REF! | #REF! | #REF! | #REF! | #REF! | #REF! | #REF! | #REF!
#REF! | #REF! | #REF! | #REF! | #REF! | #REF! | #REF! | #REF!
#REF! | #REF! | #REF! | #REF! | #REF! | #REF! | #REF! | #REF!
#REF! | #REF! | #REF! | #REF! | #REF! | #REF! | #REF! | #REF!
#REF! | #REF! | #REF! | #REF! | #REF! | #REF! | #REF! | #REF!
#REF! | #REF! | #REF! | #REF! | #REF! | #REF! | #REF! | #REF!
#REF! | #REF! | #REF! | #REF! | #REF! | #REF! | #REF! | #REF!
#REF! | #REF! | #REF! | #REF! | #REF! | #REF! | #REF! | #REF!
#REF! | #REF! | #REF! | #REF! | #REF! | #REF! | #REF! | #REF!
#REF! | #REF! | #REF! | #REF! | #REF! | #REF! | #REF! | #REF!
#REF! | #REF! | #REF! | #REF! | #REF! | #REF! | #REF! | #REF!
#REF! | #REF! | #REF! | #REF! | #REF! | #REF! | #REF! | #REF!
#REF! | #REF! | #REF! | #REF! | #REF! | #REF! | #REF! | #REF!
#REF! | #REF! | #REF! | #REF! | #REF! | #REF! | #REF! | #REF!
#REF! | #REF! | #REF! | #REF! | #REF! | #REF! | #REF! | #REF!
#REF! | #REF! | #REF! | #REF! | #REF! | #REF! | #REF! | #REF!
#REF! | #REF! | #REF! | #REF! | #REF! | #REF! | #REF! | #REF!
#REF! | #REF! | #REF! | #REF! | #REF! | #REF! | #REF! | #REF!
#REF! | #REF! | #REF! | #REF! | #REF! | #REF! | #REF! | #REF!
#REF! | #REF! | #REF! | #REF! | #REF! | #REF! | #REF! | #REF!
#REF! | #REF! | #REF! | #REF! | #REF! | #REF! | #REF! | #REF!
#REF! | #REF! | #REF! | #REF! | #REF! | #REF! | #REF! | #REF!
#REF! | #REF! | #REF! | #REF! | #REF! | #REF! | #REF! | #REF!
#REF! | #REF! | #REF! | #REF! | #REF! | #REF! | #REF! | #REF!
#REF! | #REF! | #REF! | #REF! | #REF! | #REF! | #REF! | #REF!
#REF! | #REF! | #REF! | #REF! | #REF! | #REF! | #REF! | #REF!
#REF! | #REF! | #REF! | #REF! | #REF! | #REF! | #REF! | #REF!
#REF! | #REF! | #REF! | #REF! | #REF! | #REF! | #REF! | #REF!
#REF! | #REF! | #REF! | #REF! | #REF! | #REF! | #REF! | #REF!
#REF! | #REF! | #REF! | #REF! | #REF! | #REF! | #REF! | #REF!
#REF! | #REF! | #REF! | #REF! | #REF! | #REF! | #REF! | #REF!
#REF! | #REF! | #REF! | #REF! | #REF! | #REF! | #REF! | #REF!
#REF! | #REF! | #REF! | #REF! | #REF! | #REF! | #REF! | #REF!
#REF! | #REF! | #REF! | #REF! | #REF! | #REF! | #REF! | #REF!
#REF! | #REF! | #REF! | #REF! | #REF! | #REF! | #REF! | #REF!
#REF! | #REF! | #REF! | #REF! | #REF! | #REF! | #REF! | #REF!
#REF! | #REF! | #REF! | #REF! | #REF! | #REF! | #REF! | #REF!
#REF! | #REF! | #REF! | #REF! | #REF! | #REF! | #REF! | #REF!
#REF! | #REF! | #REF! | #REF! | #REF! | #REF! | #REF! | #REF!
#REF! | #REF! | #REF! | #REF! | #REF! | #REF! | #REF! | #REF!
#REF! | #REF! | #REF! | #REF! | #REF! | #REF! | #REF! | #REF!
#REF! | #REF! | #REF! | #REF! | #REF! | #REF! | #REF! | #REF!
#REF! | #REF! | #REF! | #REF! | #REF! | #REF! | #REF! | #REF!
#REF! | #REF! | #REF! | #REF! | #REF! | #REF! | #REF! | #REF!
#REF! | #REF! | #REF! | #REF! | #REF! | #REF! | #REF! | #REF!
#REF! | #REF! | #REF! | #REF! | #REF! | #REF! | #REF! | #REF!
#REF! | #REF! | #REF! | #REF! | #REF! | #REF! | #REF! | #REF!
#REF! | #REF! | #REF! | #REF! | #REF! | #REF! | #REF! | #REF!
#REF! | #REF! | #REF! | #REF! | #REF! | #REF! | #REF! | #REF!
#REF! | #REF! | #REF! | #REF! | #REF! | #REF! | #REF! | #REF!
#REF! | #REF! | #REF! | #REF! | #REF! | #REF! | #REF! | #REF!
#REF! | #REF! | #REF! | #REF! | #REF! | #REF! | #REF! | #REF!
#REF! | #REF! | #REF! | #REF! | #REF! | #REF! | #REF! | #REF!
#REF! | #REF! | #REF! | #REF! | #REF! | #REF! | #REF! | #REF!
#REF! | #REF! | #REF! | #REF! | #REF! | #REF! | #REF! | #REF!
#REF! | #REF! | #REF! | #REF! | #REF! | #REF! | #REF! | #REF!
#REF! | #REF! | #REF! | #REF! | #REF! | #REF! | #REF! | #REF!
#REF! | #REF! | #REF! | #REF! | #REF! | #REF! | #REF! | #REF!
#REF! | #REF! | #REF! | #REF! | #REF! | #REF! | #REF! | #REF!
#REF! | #REF! | #REF! | #REF! | #REF! | #REF! | #REF! | #REF!
#REF! | #REF! | #REF! | #REF! | #REF! | #REF! | #REF! | #REF!

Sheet: ModulePCB
University | City, University of London |  |  |  |  |  |  |  | Car # | 11 |  | Asm Cost | #DIV/0!
System | Battery |  |  |  |  |  |  |  |  |  |  | Qty | 90
Assembly | Module PCB |  |  |  |  |  |  |  | FileLink1
P/N Base | A3421 |  |  |  |  |  |  |  | FileLink2 |  |  | Extended Cost | #DIV/0!
Suffix | AA |  |  |  |  |  |  |  | FileLink3
Details | Steps for assembling each of the 90 module pcbs after fabrication along with associated costs
ItemOrder | Part | Part Cost | Quantity | Sub Total
 | Custom PCB (contract fabrication) | $0.55 | 1 | $0.550
 | 20 Ohm resistor | $0.10 | 1 | $0.100
 | 10 microfarad capacitor | $0.10 | 1 | $0.100
 | 10 microhenry inductor | $0.10 | 1 | $0.100
 | 4.7 microfarad capacitor | $0.10 | 1 | $0.100
 | 125 kiloohm resistor | $0.10 | 1 | $0.100
 | 385 kiloohm resistor | $0.10 | 1 | $0.100
 | 8 Channel analog multiplexer | $0.20 | 1 | $0.199
 | DC-DC buck converter | $0.51 | 1 | $0.505
 |  |  |  | $0.000
 |  |  | Sub Total | $1.854
ItemOrder | Material | Use | UnitCost | Size1 | Unit1 | Size2 | Unit2 | Area Name | Area | Length | Density | Quantity | Sub Total
10 | Pin Headers |  | $1.00 | 40 | rows |  |  |  |  |  |  | 1 | $1.00
 |  |  |  |  |  |  |  |  |  |  |  |  | $0.00
 |  |  |  |  |  |  |  |  |  |  |  | Sub Total | $1.000
ItemOrder | Process | Use | UnitCost | Unit | Quantity | Multiplier | Mult. Val. | Sub Total
1 | Divide Pin headers | female 1row 3 pin straight pin header |  |  |  |  |  | $0.00
2 | Divide Pin headers | Male 1 row 5 pin straight pin header |  |  |  |  |  | $0.00
3 | Divide Pin headers | female 1row 2 pin straight pin header |  |  |  |  |  | $0.00
4 | Solder header #1 |  |  |  |  |  |  | $0.00
5 | Solder header #2 |  |  |  |  |  |  | $0.00
6 | Solder header #3 |  |  |  |  |  |  | $0.00
7 | Solder Mux IC |  |  |  |  |  |  | $0.00
8 | Solder Buck Converter |  |  |  |  |  |  | $0.00
9 | Solder Resistors |  |  |  |  |  |  | $0.00
10 | Solder Capacitors |  |  |  |  |  |  | $0.00
11 | Solder Inductor |  |  |  |  |  |  | $0.00
 |  |  |  |  |  |  |  | $0.00
 |  |  |  |  |  |  |  | Sub Total | 0
ItemOrder | Fastener | Use | UnitCost | Size1 | Unit1 | Size2 | Unit2 | Quantity | Sub Total
 |  |  |  |  |  |  |  |  | $0.00
 |  |  |  |  |  |  |  | Sub Total | $0.00
ItemOrder | Tooling | Use | UnitCost | Unit | Quantity | PVF | FractionIncluded | Sub Total
 |  |  |  |  |  |  |  | #DIV/0!
 |  |  |  |  |  |  |  | #DIV/0!
 |  |  |  |  |  |  | Sub Total | #DIV/0!

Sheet: ModuleAssembly
University | City, University of London |  |  |  |  |  |  |  | Car # | 11 |  | Asm Cost | #DIV/0!
System | Suspension |  |  |  |  |  |  |  |  |  |  | Qty | 90
Assembly | GadgetAsm |  |  |  |  |  |  |  | FileLink1
P/N Base | A3421 |  |  |  |  |  |  |  | FileLink2 |  |  | Extended Cost | #DIV/0!
Suffix | AA |  |  |  |  |  |  |  | FileLink3
Details | Text describing the assembly, especially unique content
ItemOrder | Part | Part Cost | Quantity | Sub Total
 | Assembled Cell |  | 10 | $0.000
 | Module PCB |  | 1 | $0.000
 | Copper Busbar |  |  | $0.000
 | LMT84 Temperature Sensor | $0.30 | 8 | $2.400
 |  |  |  | $0.000
 |  |  | Sub Total | $2.400
ItemOrder | Material | Use | UnitCost | Size1 | Unit1 | Size2 | Unit2 | Area Name | Area | Length | Density | Quantity | Sub Total
10 | Glue |  | $100.00 |  | kg |  |  | Bar 50mm Square | 2500 | 200.00 | 3.50 | 1e-05 | $1750.00
 | Dupont Nomex Paper | For Electrical Insulation between PCB and cell terminal |  |  |  |  |  |  |  |  |  |  | $0.00
 |  |  |  |  |  |  |  |  |  |  |  | Sub Total | $1750.000
ItemOrder | Process | Use | UnitCost | Unit | Quantity | Multiplier | Mult. Val. | Sub Total
 | Clip Cells together to form module string |  |  |  |  |  |  | $0.00
 | Solder Copper busbar to cell tabs
 | Cover negative terminal with nomex paper
 | Glue Temperature sensors on negative busbar
 | Slot in PCBs at negative terminal with headers to receive temp sensor leads
 | Screw in PCB
 |  |  |  |  |  |  |  | $0.00
 |  |  |  |  |  |  |  | Sub Total | 0
ItemOrder | Fastener | Use | UnitCost | Size1 | Unit1 | Size2 | Unit2 | Quantity | Sub Total
 | M3*6 Screws | To hold PCB in place |  |  |  |  |  |  | $0.00
 |  |  |  |  |  |  |  |  | $0.00
 |  |  |  |  |  |  |  | Sub Total | $0.00
ItemOrder | Tooling | Use | UnitCost | Unit | Quantity | PVF | FractionIncluded | Sub Total
 |  |  |  |  |  |  |  | #DIV/0!
 |  |  |  |  |  |  |  | #DIV/0!
 |  |  |  |  |  |  | Sub Total | #DIV/0!

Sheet: SectionPCB
University | City, University of London |  |  |  |  |  |  |  | Car # | 11 |  | Asm Cost | $1768.06
System | Suspension |  |  |  |  |  |  |  |  |  |  | Qty | 10
Assembly | GadgetAsm |  |  |  |  |  |  |  | FileLink1
P/N Base | A3421 |  |  |  |  |  |  |  | FileLink2 |  |  | Extended Cost | $17680.60
Suffix | AA |  |  |  |  |  |  |  | FileLink3
Details | Text describing the assembly, especially unique content
ItemOrder | Part | Part Cost | Quantity | Sub Total
 | Printed Circuit board | $3.30 | 1 | $3.300
 | Analog Front End BMS section protection IC | $5.03 | 1 | $5.030
 | CEDV Li-ion Gas guage | $3.11 | 1 | $3.110
 | High Voltage Front End charge/discharge high side NFET | $1.62 | 1 | $1.620
 |  |  |  | $0.000
 |  |  |  | $0.000
 |  |  |  | $0.000
 |  |  |  | $0.000
 |  |  |  | $0.000
 |  |  | Sub Total | $13.060
ItemOrder | Material | Use | UnitCost | Size1 | Unit1 | Size2 | Unit2 | Area Name | Area | Length | Density | Quantity | Sub Total
10 | Solder wire | Optional Text | $100.00 |  | kg |  |  | Bar 50mm Square | 2500 | 200.00 | 3.50 | 1e-05 | $1750.00
 |  |  |  |  |  |  |  |  |  |  |  |  | $0.00
 |  |  |  |  |  |  |  |  |  |  |  |  | $0.00
 |  |  |  |  |  |  |  |  |  |  |  | Sub Total | $1750.000
ItemOrder | Process | Use | UnitCost | Unit | Quantity | Multiplier | Mult. Val. | Sub Total
 | Solder |  |  |  |  |  |  | $0.00
 |  |  |  |  |  |  |  | $0.00
 |  |  |  |  |  |  |  | $0.00
 |  |  |  |  |  |  |  | $0.00
 |  |  |  |  |  |  |  | Sub Total | 0
ItemOrder | Fastener | Use | UnitCost | Size1 | Unit1 | Size2 | Unit2 | Quantity | Sub Total
 |  |  |  |  |  |  |  |  | $0.00
 |  |  |  |  |  |  |  |  | $0.00
 |  |  |  |  |  |  |  |  | $0.00
 |  |  |  |  |  |  |  |  | $0.00
 |  |  |  |  |  |  |  |  | $0.00
 |  |  |  |  |  |  |  |  | $0.00
 |  |  |  |  |  |  |  |  | $0.00
 |  |  |  |  |  |  |  |  | $0.00
 |  |  |  |  |  |  |  | Sub Total | $0.00
ItemOrder | Tooling | Use | UnitCost | Unit | Quantity | PVF | FractionIncluded | Sub Total
 |  |  | $5.00 |  | 1 | 2 | 1 | $2.50
 |  |  | $5.00 |  | 1 | 2 | 1 | $2.50
 |  |  |  |  |  |  | Sub Total | 5

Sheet: SectionAssembly
University | City, University of London |  |  |  |  |  |  |  | Car # | 11 |  | Asm Cost | #DIV/0!
System | Suspension |  |  |  |  |  |  |  |  |  |  | Qty | 1
Assembly | GadgetAsm |  |  |  |  |  |  |  | FileLink1
P/N Base | A3421 |  |  |  |  |  |  |  | FileLink2 |  |  | Extended Cost | #DIV/0!
Suffix | AA |  |  |  |  |  |  |  | FileLink3
Details | Text describing the assembly, especially unique content
ItemOrder | Part | Part Cost | Quantity | Sub Total
 | Assembled Module |  | 15 | $0.000
 | SectionPCB |  | 1 | $0.000
 | Voltage Taps |  |  | $0.000
 |  |  |  | $0.000
 |  |  |  | $0.000
 |  |  |  | $0.000
 |  |  |  | $0.000
 |  |  |  | $0.000
 |  |  |  | $0.000
 |  |  | Sub Total | $0.000
ItemOrder | Material | Use | UnitCost | Size1 | Unit1 | Size2 | Unit2 | Area Name | Area | Length | Density | Quantity | Sub Total
10 | Wire for voltage taps | Optional Text | $100.00 |  | kg |  |  | Bar 50mm Square | 2500 | 200.00 | 3.50 | 1e-05 | $1750.00
20 | Nomex Paper | Insulation for PCB | $200.00 |  | unit |  |  |  |  |  |  | 1.00 | $200.00
30 | Bearing | Rocker bearing | $10.12 | 20 | mm | 40 | mm |  |  |  |  | 2.00 | $20.24
 |  |  |  |  |  |  |  |  |  |  |  |  | $0.00
 |  |  |  |  |  |  |  |  |  |  |  |  | $0.00
 |  |  |  |  |  |  |  |  |  |  |  |  | $0.00
 |  |  |  |  |  |  |  |  |  |  |  |  | $0.00
 |  |  |  |  |  |  |  |  |  |  |  |  | $0.00
 |  |  |  |  |  |  |  |  |  |  |  | Sub Total | $1970.239
ItemOrder | Process | Use | UnitCost | Unit | Quantity | Multiplier | Mult. Val. | Sub Total
 | Weld copper busbars for series connections |  |  |  |  |  |  | $0.00
 | Solder voltage taps |  |  |  |  |  |  | $0.00
 | Lay on nomex paper |  |  |  |  |  |  | $0.00
 | screw pcb in place |  |  |  |  |  |  | $0.00
 |  |  |  |  |  |  |  | $0.00
 |  |  |  |  |  |  |  | $0.00
 |  |  |  |  |  |  |  | $0.00
 |  |  |  |  |  |  |  | $0.00
 |  |  |  |  |  |  |  | Sub Total | 0
ItemOrder | Fastener | Use | UnitCost | Size1 | Unit1 | Size2 | Unit2 | Quantity | Sub Total
 | M3*6 screw | To hold pcb in place |  |  |  |  |  |  | $0.00
 |  |  |  |  |  |  |  |  | $0.00
 |  |  |  |  |  |  |  |  | $0.00
 |  |  |  |  |  |  |  |  | $0.00
 |  |  |  |  |  |  |  |  | $0.00
 |  |  |  |  |  |  |  |  | $0.00
 |  |  |  |  |  |  |  |  | $0.00
 |  |  |  |  |  |  |  |  | $0.00
 |  |  |  |  |  |  |  | Sub Total | $0.00
ItemOrder | Tooling | Use | UnitCost | Unit | Quantity | PVF | FractionIncluded | Sub Total
 |  |  |  |  |  |  |  | #DIV/0!
 |  |  |  |  |  |  |  | #DIV/0!
 |  |  |  |  |  |  | Sub Total | #DIV/0!

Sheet: BatteryBox
University | City, University of London |  |  |  |  |  |  |  | Car # | 11 |  | Asm Cost | #DIV/0!
System | Suspension |  |  |  |  |  |  |  |  |  |  | Qty | 1
Assembly | GadgetAsm |  |  |  |  |  |  |  | FileLink1
P/N Base | A3421 |  |  |  |  |  |  |  | FileLink2 |  |  | Extended Cost | #DIV/0!
Suffix | AA |  |  |  |  |  |  |  | FileLink3
Details | Text describing the assembly, especially unique content
ItemOrder | Part | Part Cost | Quantity | Sub Total
 |  |  |  | $0.000
 |  |  |  | $0.000
 |  |  |  | $0.000
 |  |  |  | $0.000
 |  |  |  | $0.000
 |  |  |  | $0.000
 |  |  |  | $0.000
 |  |  |  | $0.000
 |  |  |  | $0.000
 |  |  | Sub Total | $0.000
ItemOrder | Material | Use | UnitCost | Size1 | Unit1 | Size2 | Unit2 | Area Name | Area | Length | Density | Quantity | Sub Total
10 | Aluminium | Optional Text | $100.00 |  | kg |  |  | Bar 50mm Square | 2500 | 200.00 | 3.50 | 1e-05 | $1750.00
 |  |  |  |  |  |  |  |  |  |  |  |  | $0.00
 |  |  |  |  |  |  |  |  |  |  |  | Sub Total | $1750.000
ItemOrder | Process | Use | UnitCost | Unit | Quantity | Multiplier | Mult. Val. | Sub Total
 | Bend |  |  |  |  |  |  | $0.00
 |  |  |  |  |  |  |  | $0.00
 |  |  |  |  |  |  |  | $0.00
 |  |  |  |  |  |  |  | $0.00
 |  |  |  |  |  |  |  | $0.00
 |  |  |  |  |  |  |  | $0.00
 |  |  |  |  |  |  |  | $0.00
 |  |  |  |  |  |  |  | $0.00
 |  |  |  |  |  |  |  | Sub Total | 0
ItemOrder | Fastener | Use | UnitCost | Size1 | Unit1 | Size2 | Unit2 | Quantity | Sub Total
 |  |  |  |  |  |  |  |  | $0.00
 |  |  |  |  |  |  |  |  | $0.00
 |  |  |  |  |  |  |  |  | $0.00
 |  |  |  |  |  |  |  |  | $0.00
 |  |  |  |  |  |  |  |  | $0.00
 |  |  |  |  |  |  |  |  | $0.00
 |  |  |  |  |  |  |  |  | $0.00
 |  |  |  |  |  |  |  |  | $0.00
 |  |  |  |  |  |  |  | Sub Total | $0.00
ItemOrder | Tooling | Use | UnitCost | Unit | Quantity | PVF | FractionIncluded | Sub Total
 |  |  |  |  |  |  |  | #DIV/0!
 |  |  |  |  |  |  |  | #DIV/0!
 |  |  |  |  |  |  | Sub Total | #DIV/0!

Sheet: PackAssembly
University | City, University of London |  |  |  |  |  |  |  | Car # | 11 |  | Asm Cost | #DIV/0!
System | Suspension |  |  |  |  |  |  |  |  |  |  | Qty | 1
Assembly | GadgetAsm |  |  |  |  |  |  |  | FileLink1
P/N Base | A3421 |  |  |  |  |  |  |  | FileLink2 |  |  | Extended Cost | #DIV/0!
Suffix | AA |  |  |  |  |  |  |  | FileLink3
Details | Text describing the assembly, especially unique content
ItemOrder | Part | Part Cost | Quantity | Sub Total
 |  |  |  | $0.000
 |  |  |  | $0.000
 |  |  |  | $0.000
 |  |  |  | $0.000
 |  |  |  | $0.000
 |  |  |  | $0.000
 |  |  |  | $0.000
 |  |  |  | $0.000
 |  |  |  | $0.000
 |  |  | Sub Total | $0.000
ItemOrder | Material | Use | UnitCost | Size1 | Unit1 | Size2 | Unit2 | Area Name | Area | Length | Density | Quantity | Sub Total
10 | Unobtanium | Optional Text | $100.00 |  | kg |  |  | Bar 50mm Square | 2500 | 200.00 | 3.50 | 1e-05 | $1750.00
20 | Damper | Mono-shock front | $200.00 |  | unit |  |  |  |  |  |  | 1.00 | $200.00
30 | Bearing | Rocker bearing | $10.12 | 20 | mm | 40 | mm |  |  |  |  | 2.00 | $20.24
 |  |  |  |  |  |  |  |  |  |  |  |  | $0.00
 |  |  |  |  |  |  |  |  |  |  |  |  | $0.00
 |  |  |  |  |  |  |  |  |  |  |  |  | $0.00
 |  |  |  |  |  |  |  |  |  |  |  |  | $0.00
 |  |  |  |  |  |  |  |  |  |  |  |  | $0.00
 |  |  |  |  |  |  |  |  |  |  |  | Sub Total | $1970.239
ItemOrder | Process | Use | UnitCost | Unit | Quantity | Multiplier | Mult. Val. | Sub Total
 |  |  |  |  |  |  |  | $0.00
 |  |  |  |  |  |  |  | $0.00
 |  |  |  |  |  |  |  | $0.00
 |  |  |  |  |  |  |  | $0.00
 |  |  |  |  |  |  |  | $0.00
 |  |  |  |  |  |  |  | $0.00
 |  |  |  |  |  |  |  | $0.00
 |  |  |  |  |  |  |  | $0.00
 |  |  |  |  |  |  |  | Sub Total | 0
ItemOrder | Fastener | Use | UnitCost | Size1 | Unit1 | Size2 | Unit2 | Quantity | Sub Total
 |  |  |  |  |  |  |  |  | $0.00
 |  |  |  |  |  |  |  |  | $0.00
 |  |  |  |  |  |  |  |  | $0.00
 |  |  |  |  |  |  |  |  | $0.00
 |  |  |  |  |  |  |  |  | $0.00
 |  |  |  |  |  |  |  |  | $0.00
 |  |  |  |  |  |  |  |  | $0.00
 |  |  |  |  |  |  |  |  | $0.00
 |  |  |  |  |  |  |  | Sub Total | $0.00
ItemOrder | Tooling | Use | UnitCost | Unit | Quantity | PVF | FractionIncluded | Sub Total
 |  |  |  |  |  |  |  | #DIV/0!
 |  |  |  |  |  |  |  | #DIV/0!
 |  |  |  |  |  |  | Sub Total | #DIV/0!

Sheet: Assembly_1
University | City, University of London |  |  |  |  |  |  |  | Car # | 11 |  | Asm Cost | $1975.24
System | Suspension |  |  |  |  |  |  |  |  |  |  | Qty | 1
Assembly | GadgetAsm |  |  |  |  |  |  |  | FileLink1
P/N Base | A3421 |  |  |  |  |  |  |  | FileLink2 |  |  | Extended Cost | $1975.24
Suffix | AA |  |  |  |  |  |  |  | FileLink3
Details | Text describing the assembly, especially unique content
ItemOrder | Part | Part Cost | Quantity | Sub Total
 |  |  |  | $0.000
 |  |  |  | $0.000
 |  |  |  | $0.000
 |  |  |  | $0.000
 |  |  |  | $0.000
 |  |  |  | $0.000
 |  |  |  | $0.000
 |  |  |  | $0.000
 |  |  |  | $0.000
 |  |  | Sub Total | $0.000
ItemOrder | Material | Use | UnitCost | Size1 | Unit1 | Size2 | Unit2 | Area Name | Area | Length | Density | Quantity | Sub Total
10 | Unobtanium | Optional Text | $100.00 |  | kg |  |  | Bar 50mm Square | 2500 | 200.00 | 3.50 | 1e-05 | $1750.00
20 | Damper | Mono-shock front | $200.00 |  | unit |  |  |  |  |  |  | 1.00 | $200.00
30 | Bearing | Rocker bearing | $10.12 | 20 | mm | 40 | mm |  |  |  |  | 2.00 | $20.24
 |  |  |  |  |  |  |  |  |  |  |  |  | $0.00
 |  |  |  |  |  |  |  |  |  |  |  |  | $0.00
 |  |  |  |  |  |  |  |  |  |  |  |  | $0.00
 |  |  |  |  |  |  |  |  |  |  |  |  | $0.00
 |  |  |  |  |  |  |  |  |  |  |  |  | $0.00
 |  |  |  |  |  |  |  |  |  |  |  | Sub Total | $1970.239
ItemOrder | Process | Use | UnitCost | Unit | Quantity | Multiplier | Mult. Val. | Sub Total
 |  |  |  |  |  |  |  | $0.00
 |  |  |  |  |  |  |  | $0.00
 |  |  |  |  |  |  |  | $0.00
 |  |  |  |  |  |  |  | $0.00
 |  |  |  |  |  |  |  | $0.00
 |  |  |  |  |  |  |  | $0.00
 |  |  |  |  |  |  |  | $0.00
 |  |  |  |  |  |  |  | $0.00
 |  |  |  |  |  |  |  | Sub Total | 0
ItemOrder | Fastener | Use | UnitCost | Size1 | Unit1 | Size2 | Unit2 | Quantity | Sub Total
 |  |  |  |  |  |  |  |  | $0.00
 |  |  |  |  |  |  |  |  | $0.00
 |  |  |  |  |  |  |  |  | $0.00
 |  |  |  |  |  |  |  |  | $0.00
 |  |  |  |  |  |  |  |  | $0.00
 |  |  |  |  |  |  |  |  | $0.00
 |  |  |  |  |  |  |  |  | $0.00
 |  |  |  |  |  |  |  |  | $0.00
 |  |  |  |  |  |  |  | Sub Total | $0.00
ItemOrder | Tooling | Use | UnitCost | Unit | Quantity | PVF | FractionIncluded | Sub Total
 |  |  | $5.00 |  | 1 | 2 | 1 | $2.50
 |  |  | $5.00 |  | 1 | 2 | 1 | $2.50
 |  |  |  |  |  |  | Sub Total | 5
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

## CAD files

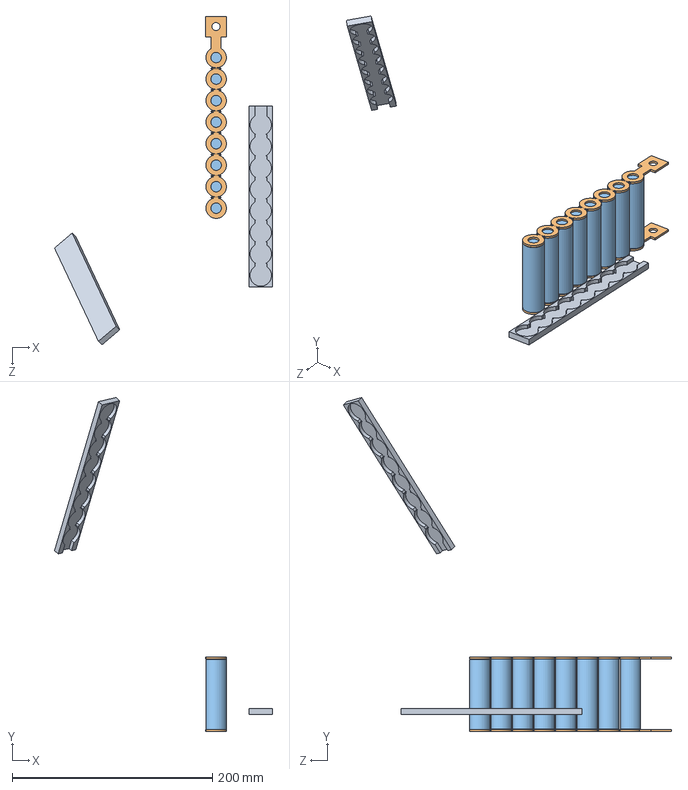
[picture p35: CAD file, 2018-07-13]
20700/BatteryAssemblyJustBusbar.SLDASM
217.9 x 333.7 x 328.2 mm
BatteryCover_Draft4 x 2
BatteryBusbar_Draft x 2
20700ACell x 8

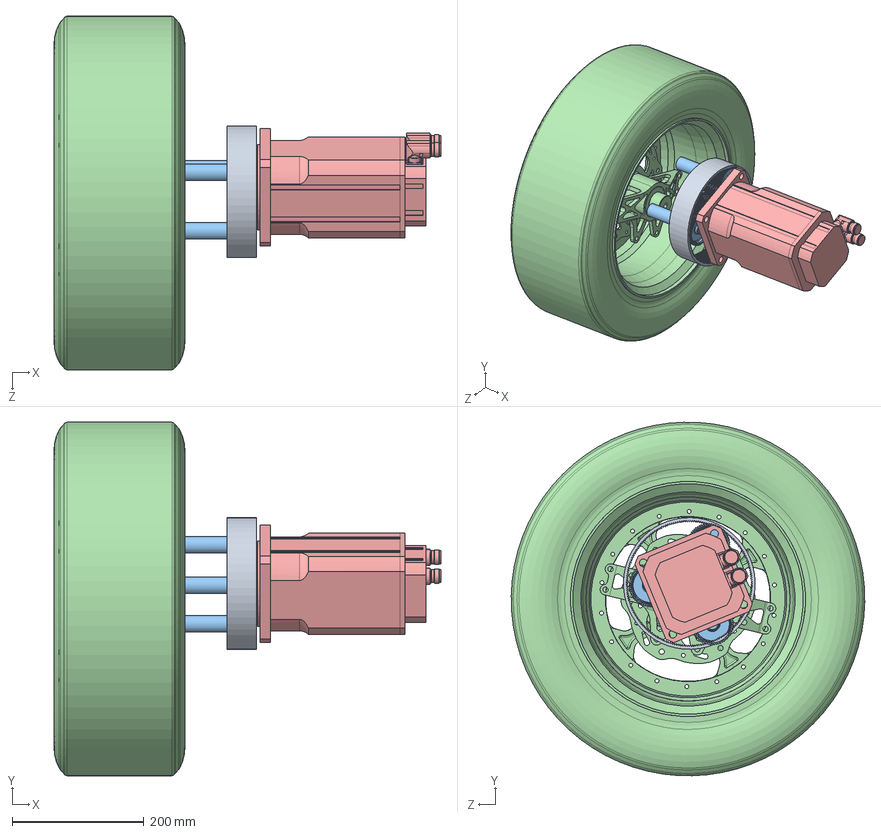
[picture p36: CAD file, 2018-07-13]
18650/In-wheel-Motor-with_transmission_is_the_main_file/In-wheel-Motor-with-tranmission.SLDASM
587.6 x 536.8 x 536.9 mm
Ring Gear
Sun Gear Final
Planet x 3
Wheel
TGN5-1600-KE1 (2)

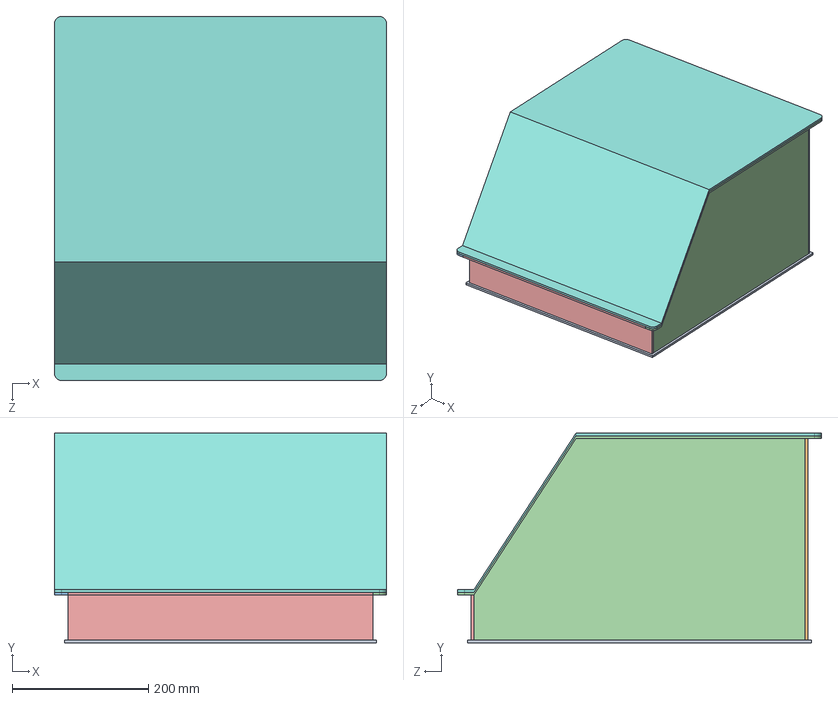
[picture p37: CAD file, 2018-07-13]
18650/BatteryBoxWithCover.SLDASM
488.0 x 308.0 x 535.0 mm
box_base
box_back
box_side
box_sidemirrored
box_front
box_inner x 5
box_frontdivider
box_TopCover

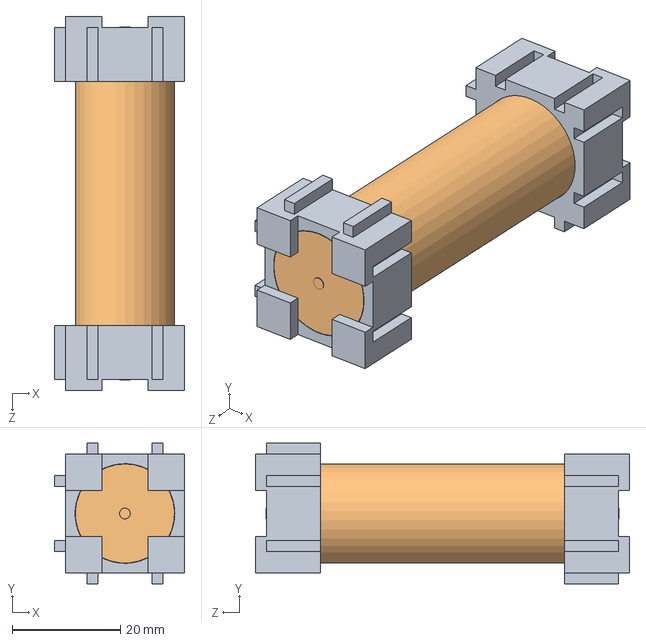
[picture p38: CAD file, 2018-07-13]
18650/BatteryWithCap.SLDASM
24.0 x 26.0 x 69.0 mm
EndCap x 2
HB2

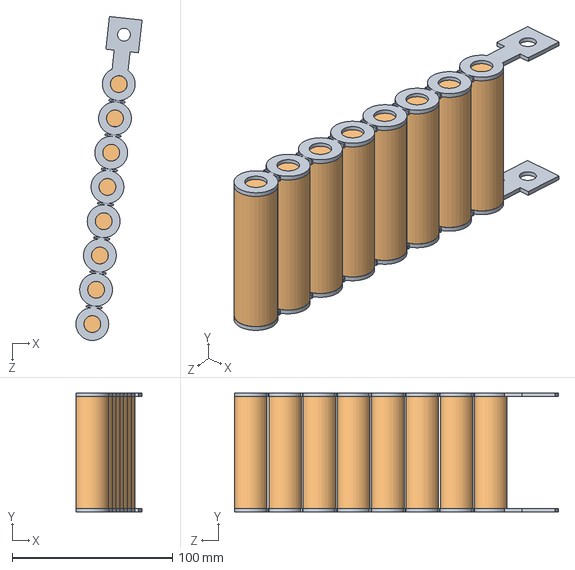
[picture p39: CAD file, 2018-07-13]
20700/BatteryAssemblywithoutCover.SLDASM
41.3 x 74.0 x 202.0 mm
BatteryBusbar_Draft x 2
20700ACell x 8

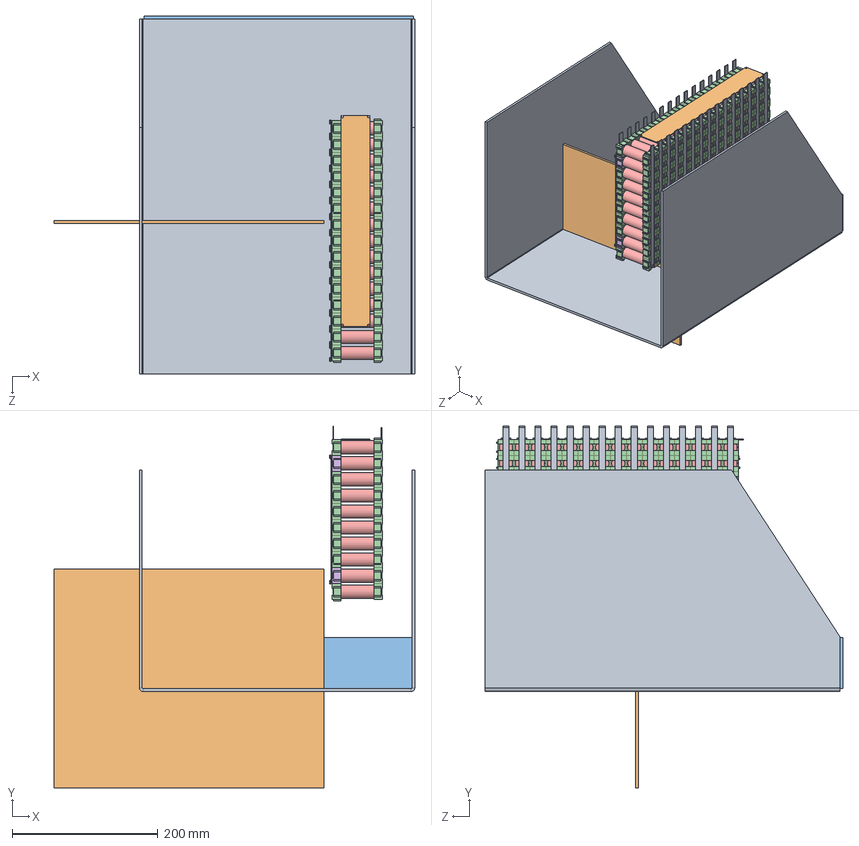
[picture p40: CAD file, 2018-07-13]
18650/BatteryBoxWithBatteries.SLDASM
494.8 x 496.0 x 491.0 mm
BatteryBoxStart
box_back
box_front
EndCap x 270
HB2 x 150
EndCapWithM3 x 30
DummyPCB x 15
pan slot head_am x 60
CopperConductor x 30
DummyPCBForSection

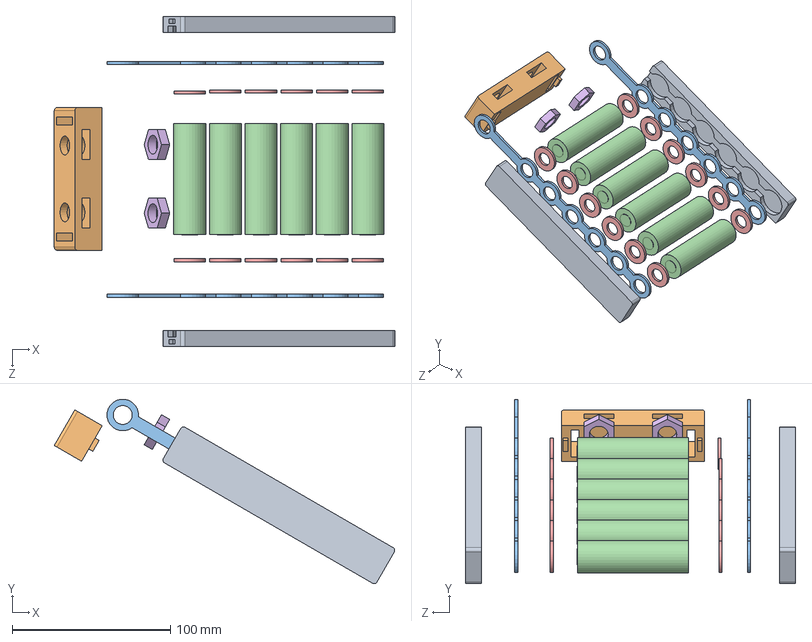
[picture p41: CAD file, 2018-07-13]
20700/BatteryAssemblyDraft2Exploded.SLDASM
215.3 x 116.6 x 208.6 mm
BatteryCover_Draft6 x 2
BatteryTopCover
BatteryBusbar_Draft3 x 2
20700ACell x 6
PlasticWasher x 12
HexNut x 2

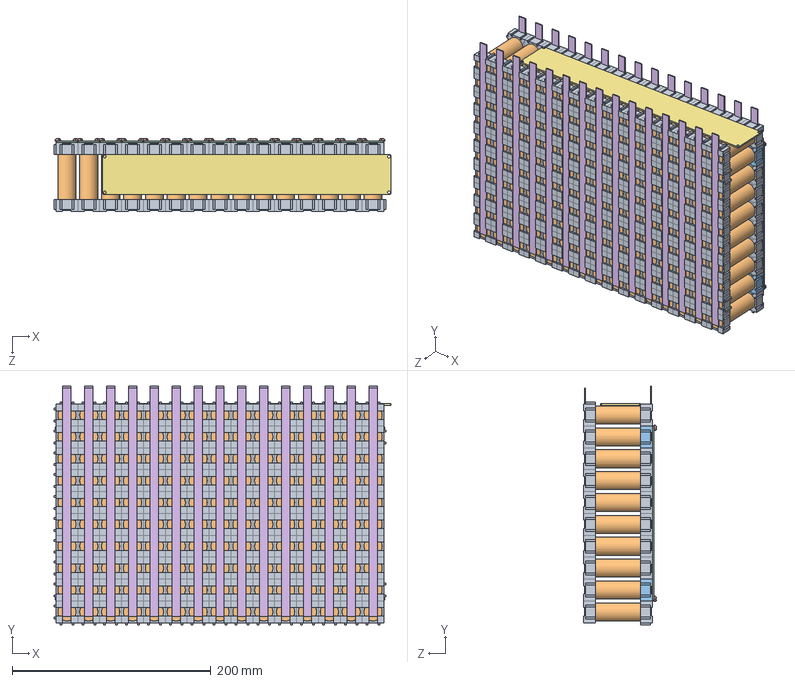
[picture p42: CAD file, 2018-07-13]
18650/SectionAssembly.SLDASM
339.0 x 240.0 x 73.0 mm
EndCap x 270
HB2 x 150
EndCapWithM3 x 30
DummyPCB x 15
pan slot head_am x 60
CopperConductor x 30
DummyPCBForSection

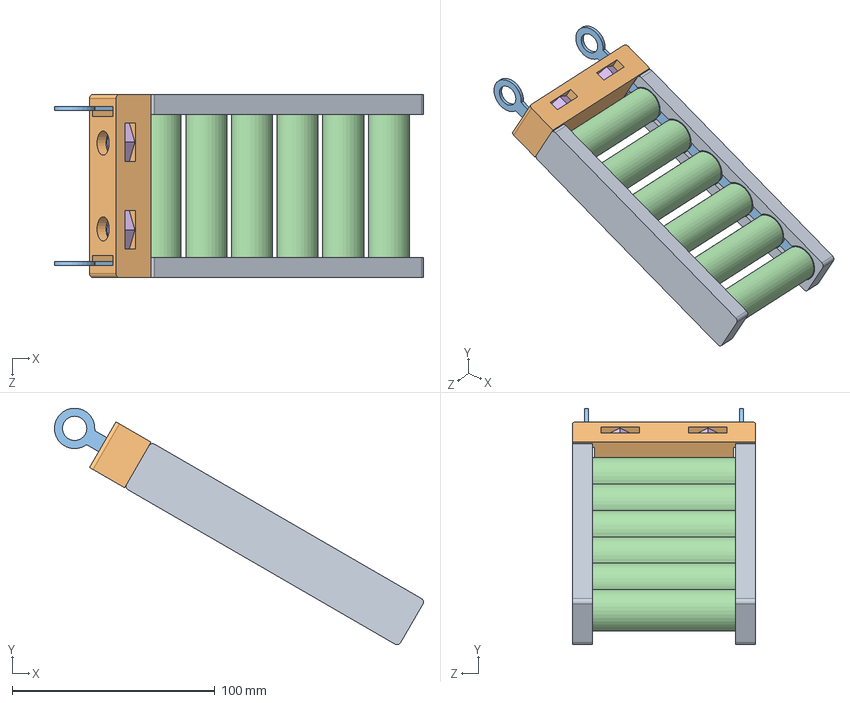
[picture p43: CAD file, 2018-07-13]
20700/BatteryAssemblyDraft2.SLDASM
181.9 x 116.6 x 90.3 mm
BatteryCover_Draft6 x 2
BatteryTopCover
BatteryBusbar_Draft3 x 2
20700ACell x 6
PlasticWasher x 12
HexNut x 2

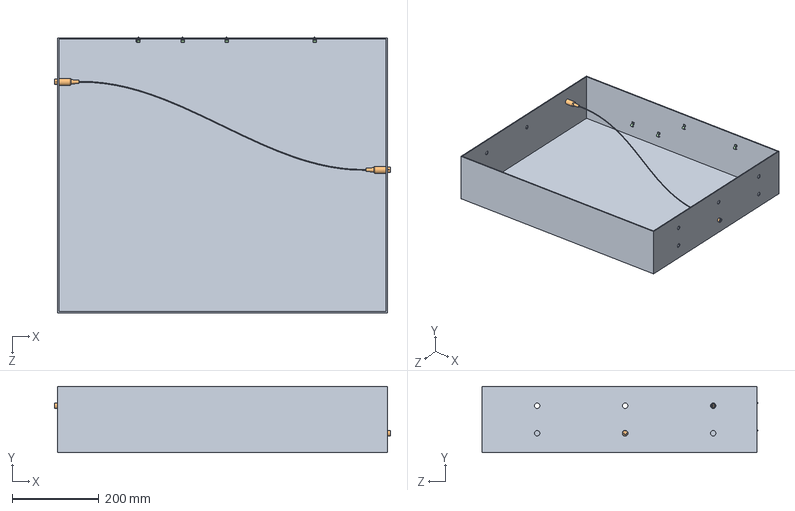
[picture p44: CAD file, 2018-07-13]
20700/top_assy.sldasm
775.7 x 152.4 x 636.6 mm
electronic housing
plug-5pindin x 2
Cable^Harness_2-top_assy
90_richco_hurc-4-01-clip x 4

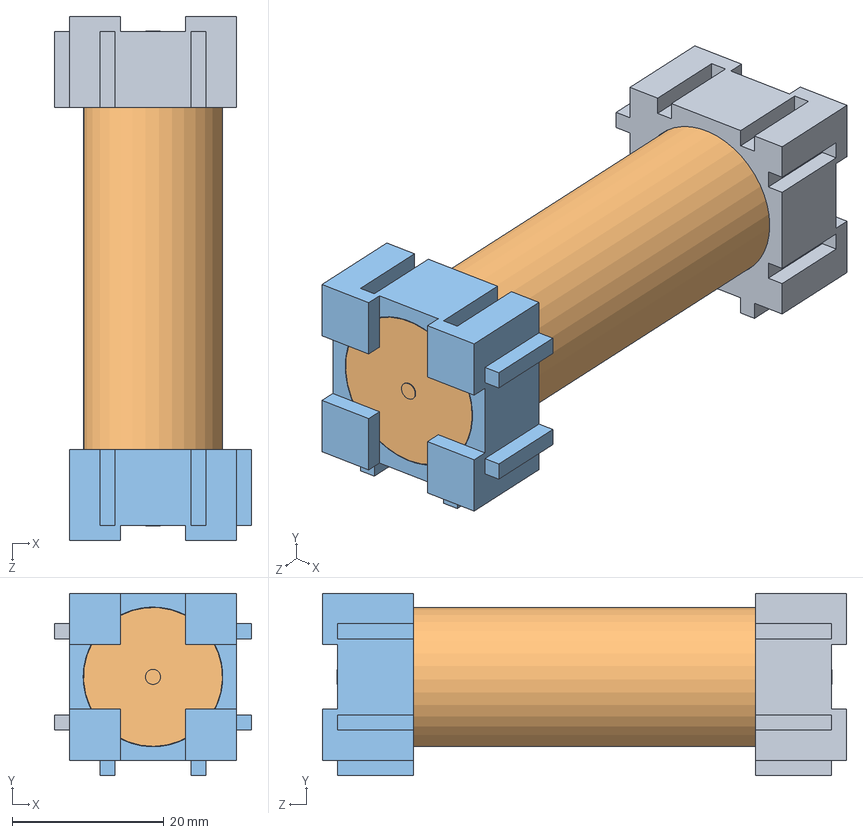
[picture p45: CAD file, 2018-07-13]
18650/ModuleWithM3EndCap.SLDASM
26.0 x 24.0 x 69.0 mm
EndCapWithM3
HB2
EndCap

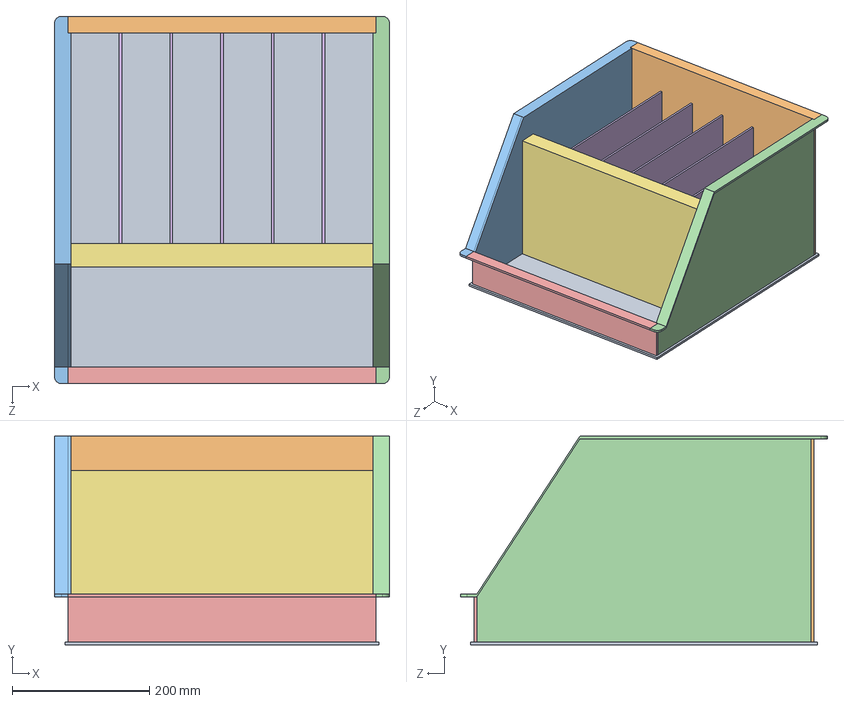
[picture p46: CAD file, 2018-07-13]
18650/BatteryBox.SLDASM
488.0 x 304.0 x 535.0 mm
box_base
box_back
box_side
box_sidemirrored
box_front
box_inner x 5
box_frontdivider

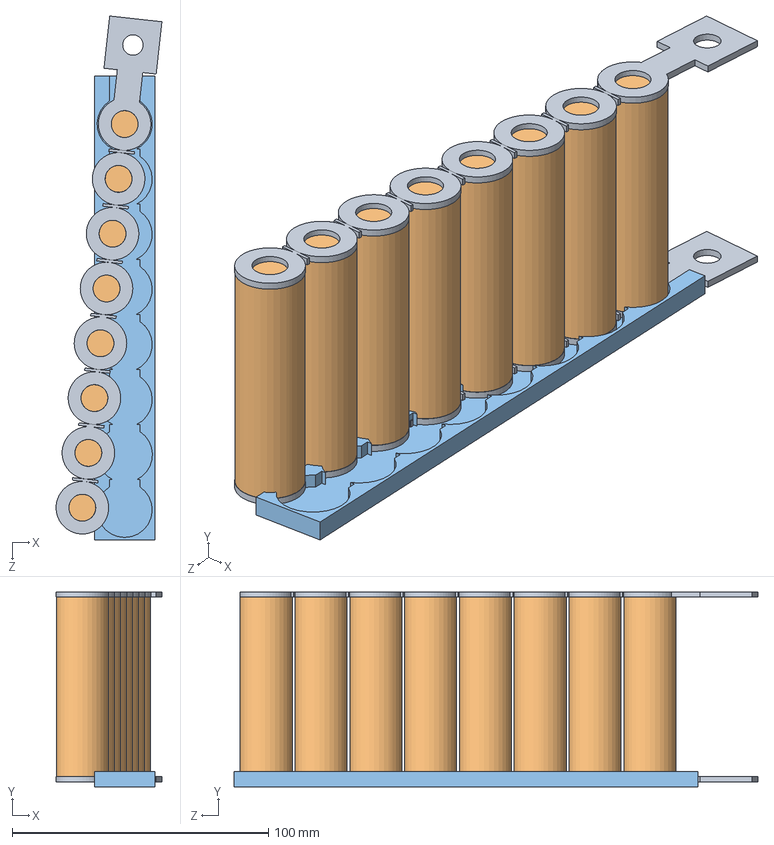
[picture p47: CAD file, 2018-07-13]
20700/BatteryAssembly.SLDASM
41.3 x 76.0 x 204.3 mm
BatteryBusbar_Draft x 2
20700ACell x 8
BatteryCover_Draft4

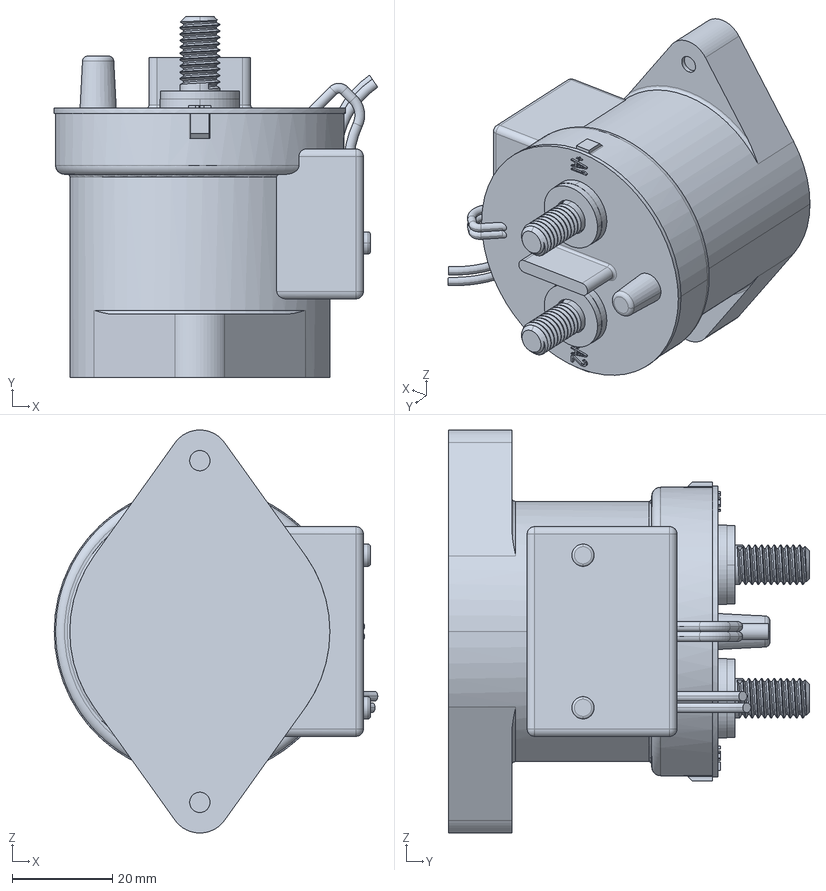
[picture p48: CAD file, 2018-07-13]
18650/AIR/c-1618002-7-m-3d.stp
64.6 x 72.2 x 80.5 mm

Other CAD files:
20700/Assem5.SLDASM
18650/In-wheel-Motor-with_transmission_is_the_main_file/Harness_1-In-wheel-Motor-with-tranmission.sldasm
20700/Assem4.SLDASM
20700/Harness_2-top_assy.sldasm
18650/18650Module.SLDASM
18650/AIR/c-1618002-7-m-3d.SLDPRT
18650/BatteryBoxStart.SLDPRT
18650/CopperConductor.SLDPRT
18650/DummyPCB.SLDPRT
18650/DummyPCBForSection.SLDPRT
18650/EndCap.SLDPRT
18650/EndCapWithM3.SLDPRT
18650/HB2.SLDPRT
18650/In-wheel-Motor-with_transmission_is_the_main_file/ID_1.sldprt
18650/In-wheel-Motor-with_transmission_is_the_main_file/ID_1_2.sldprt
18650/In-wheel-Motor-with_transmission_is_the_main_file/ID_1_3.sldprt
18650/In-wheel-Motor-with_transmission_is_the_main_file/ID_1_4.sldprt
18650/In-wheel-Motor-with_transmission_is_the_main_file/Planet.SLDPRT
18650/In-wheel-Motor-with_transmission_is_the_main_file/Ring Gear.SLDPRT
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

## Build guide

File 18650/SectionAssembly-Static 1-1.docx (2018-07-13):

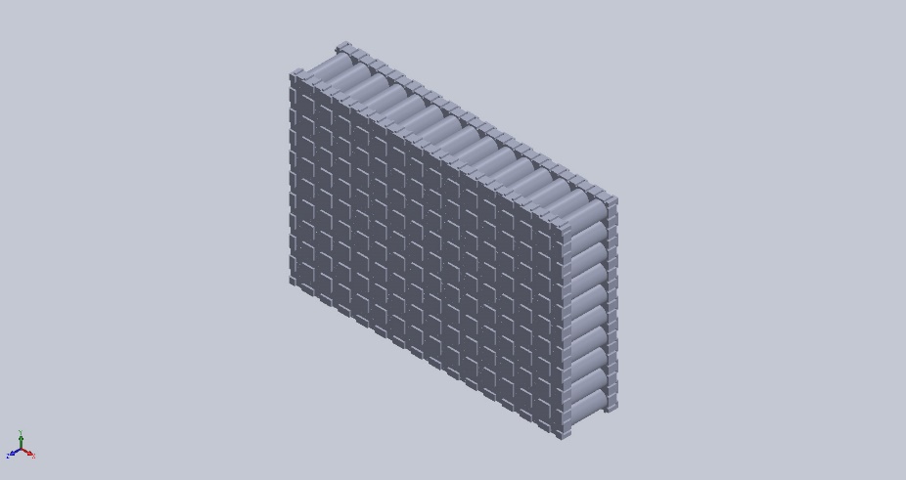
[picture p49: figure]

Simulation of SectionAssembly

Date: Tuesday, February 27, 2018
Designer: Solidworks

Study name: Static 1

Analysis type: Static
Description No Data

# Assumptions

# Model Information

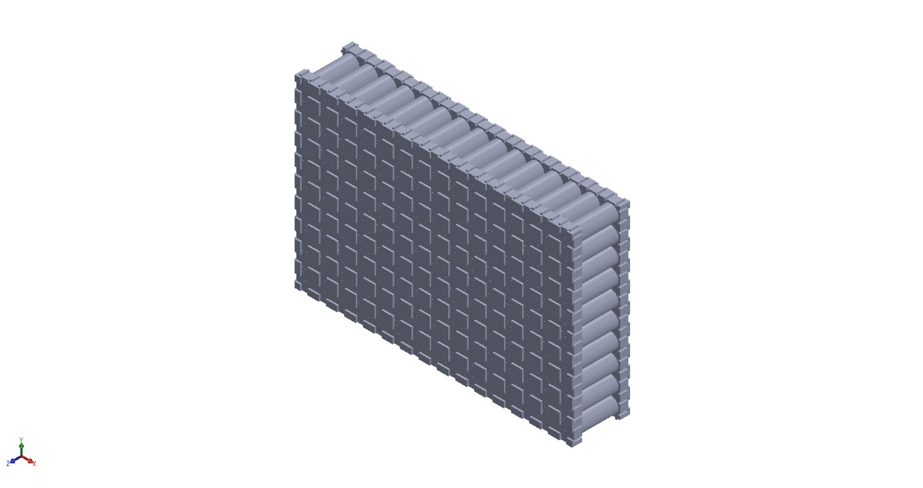
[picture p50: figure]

Model name: SectionAssembly

Current Configuration: Default

Solid Bodies
Document Name and Reference | Treated As | Volumetric Properties | Document Path/Date Modified
Boss-Extrude4 | Solid Body | Mass:2.54546e-006 kg Volume:2.54546e-006 m^3 Density:1 kg/m^3 Weight:2.49455e-005 N | C:\Users\fenobus\OneDrive - City, University of London\SolidworksFiles\fs\18650\EndCap.SLDPRT Feb 26 18:34:28 2018
Boss-Extrude4 | Solid Body | Mass:2.54546e-006 kg Volume:2.54546e-006 m^3 Density:1 kg/m^3 Weight:2.49455e-005 N | C:\Users\fenobus\OneDrive - City, University of London\SolidworksFiles\fs\18650\EndCap.SLDPRT Feb 26 18:34:28 2018
Boss-Extrude3 | Solid Body | Mass:1.70971e-005 kg Volume:1.70971e-005 m^3 Density:1 kg/m^3 Weight:0.000167551 N | C:\Users\fenobus\OneDrive - City, University of London\SolidworksFiles\fs\18650\HB2.SLDPRT Feb 25 17:30:42 2018
Boss-Extrude4 | Solid Body | Mass:2.54546e-006 kg Volume:2.54546e-006 m^3 Density:1 kg/m^3 Weight:2.49455e-005 N | C:\Users\fenobus\OneDrive - City, University of London\SolidworksFiles\fs\18650\EndCap.SLDPRT Feb 26 18:34:28 2018
Boss-Extrude4 | Solid Body | Mass:2.54546e-006 kg Volume:2.54546e-006 m^3 Density:1 kg/m^3 Weight:2.49455e-005 N | C:\Users\fenobus\OneDrive - City, University of London\SolidworksFiles\fs\18650\EndCap.SLDPRT Feb 26 18:34:28 2018
Boss-Extrude3 | Solid Body | Mass:1.70971e-005 kg Volume:1.70971e-005 m^3 Density:1 kg/m^3 Weight:0.000167551 N | C:\Users\fenobus\OneDrive - City, University of London\SolidworksFiles\fs\18650\HB2.SLDPRT Feb 25 17:30:42 2018
Boss-Extrude4 | Solid Body | Mass:2.54546e-006 kg Volume:2.54546e-006 m^3 Density:1 kg/m^3 Weight:2.49455e-005 N | C:\Users\fenobus\OneDrive - City, University of London\SolidworksFiles\fs\18650\EndCap.SLDPRT Feb 26 18:34:28 2018
Boss-Extrude4 | Solid Body | Mass:2.54546e-006 kg Volume:2.54546e-006 m^3 Density:1 kg/m^3 Weight:2.49455e-005 N | C:\Users\fenobus\OneDrive - City, University of London\SolidworksFiles\fs\18650\EndCap.SLDPRT Feb 26 18:34:28 2018
Boss-Extrude3 | Solid Body | Mass:1.70971e-005 kg Volume:1.70971e-005 m^3 Density:1 kg/m^3 Weight:0.000167551 N | C:\Users\fenobus\OneDrive - City, University of London\SolidworksFiles\fs\18650\HB2.SLDPRT Feb 25 17:30:42 2018
Boss-Extrude4 | Solid Body | Mass:2.54546e-006 kg Volume:2.54546e-006 m^3 Density:1 kg/m^3 Weight:2.49455e-005 N | C:\Users\fenobus\OneDrive - City, University of London\SolidworksFiles\fs\18650\EndCap.SLDPRT Feb 26 18:34:28 2018
Boss-Extrude4 | Solid Body | Mass:2.54546e-006 kg Volume:2.54546e-006 m^3 Density:1 kg/m^3 Weight:2.49455e-005 N | C:\Users\fenobus\OneDrive - City, University of London\SolidworksFiles\fs\18650\EndCap.SLDPRT Feb 26 18:34:28 2018
Boss-Extrude3 | Solid Body | Mass:1.70971e-005 kg Volume:1.70971e-005 m^3 Density:1 kg/m^3 Weight:0.000167551 N | C:\Users\fenobus\OneDrive - City, University of London\SolidworksFiles\fs\18650\HB2.SLDPRT Feb 25 17:30:42 2018
Boss-Extrude4 | Solid Body | Mass:2.54546e-006 kg Volume:2.54546e-006 m^3 Density:1 kg/m^3 Weight:2.49455e-005 N | C:\Users\fenobus\OneDrive - City, University of London\SolidworksFiles\fs\18650\EndCap.SLDPRT Feb 26 18:34:28 2018
Boss-Extrude4 | Solid Body | Mass:2.54546e-006 kg Volume:2.54546e-006 m^3 Density:1 kg/m^3 Weight:2.49455e-005 N | C:\Users\fenobus\OneDrive - City, University of London\SolidworksFiles\fs\18650\EndCap.SLDPRT Feb 26 18:34:28 2018
Boss-Extrude3 | Solid Body | Mass:1.70971e-005 kg Volume:1.70971e-005 m^3 Density:1 kg/m^3 Weight:0.000167551 N | C:\Users\fenobus\OneDrive - City, University of London\SolidworksFiles\fs\18650\HB2.SLDPRT Feb 25 17:30:42 2018
Boss-Extrude4 | Solid Body | Mass:2.54546e-006 kg Volume:2.54546e-006 m^3 Density:1 kg/m^3 Weight:2.49455e-005 N | C:\Users\fenobus\OneDrive - City, University of London\SolidworksFiles\fs\18650\EndCap.SLDPRT Feb 26 18:34:28 2018
Boss-Extrude4 | Solid Body | Mass:2.54546e-006 kg Volume:2.54546e-006 m^3 Density:1 kg/m^3 Weight:2.49455e-005 N | C:\Users\fenobus\OneDrive - City, University of London\SolidworksFiles\fs\18650\EndCap.SLDPRT Feb 26 18:34:28 2018
Boss-Extrude3 | Solid Body | Mass:1.70971e-005 kg Volume:1.70971e-005 m^3 Density:1 kg/m^3 Weight:0.000167551 N | C:\Users\fenobus\OneDrive - City, University of London\SolidworksFiles\fs\18650\HB2.SLDPRT Feb 25 17:30:42 2018
Boss-Extrude4 | Solid Body | Mass:2.54546e-006 kg Volume:2.54546e-006 m^3 Density:1 kg/m^3 Weight:2.49455e-005 N | C:\Users\fenobus\OneDrive - City, University of London\SolidworksFiles\fs\18650\EndCap.SLDPRT Feb 26 18:34:28 2018
Boss-Extrude4 | Solid Body | Mass:2.54546e-006 kg Volume:2.54546e-006 m^3 Density:1 kg/m^3 Weight:2.49455e-005 N | C:\Users\fenobus\OneDrive - City, University of London\SolidworksFiles\fs\18650\EndCap.SLDPRT Feb 26 18:34:28 2018
Boss-Extrude3 | Solid Body | Mass:1.70971e-005 kg Volume:1.70971e-005 m^3 Density:1 kg/m^3 Weight:0.000167551 N | C:\Users\fenobus\OneDrive - City, University of London\SolidworksFiles\fs\18650\HB2.SLDPRT Feb 25 17:30:42 2018
Boss-Extrude4 | Solid Body | Mass:2.54546e-006 kg Volume:2.54546e-006 m^3 Density:1 kg/m^3 Weight:2.49455e-005 N | C:\Users\fenobus\OneDrive - City, University of London\SolidworksFiles\fs\18650\EndCap.SLDPRT Feb 26 18:34:28 2018
Boss-Extrude4 | Solid Body | Mass:2.54546e-006 kg Volume:2.54546e-006 m^3 Density:1 kg/m^3 Weight:2.49455e-005 N | C:\Users\fenobus\OneDrive - City, University of London\SolidworksFiles\fs\18650\EndCap.SLDPRT Feb 26 18:34:28 2018
Boss-Extrude3 | Solid Body | Mass:1.70971e-005 kg Volume:1.70971e-005 m^3 Density:1 kg/m^3 Weight:0.000167551 N | C:\Users\fenobus\OneDrive - City, University of London\SolidworksFiles\fs\18650\HB2.SLDPRT Feb 25 17:30:42 2018
Boss-Extrude4 | Solid Body | Mass:2.54546e-006 kg Volume:2.54546e-006 m^3 Density:1 kg/m^3 Weight:2.49455e-005 N | C:\Users\fenobus\OneDrive - City, University of London\SolidworksFiles\fs\18650\EndCap.SLDPRT Feb 26 18:34:28 2018
Boss-Extrude4 | Solid Body | Mass:2.54546e-006 kg Volume:2.54546e-006 m^3 Density:1 kg/m^3 Weight:2.49455e-005 N | C:\Users\fenobus\OneDrive - City, University of London\SolidworksFiles\fs\18650\EndCap.SLDPRT Feb 26 18:34:28 2018
Boss-Extrude3 | Solid Body | Mass:1.70971e-005 kg Volume:1.70971e-005 m^3 Density:1 kg/m^3 Weight:0.000167551 N | C:\Users\fenobus\OneDrive - City, University of London\SolidworksFiles\fs\18650\HB2.SLDPRT Feb 25 17:30:42 2018
Boss-Extrude4 | Solid Body | Mass:2.54546e-006 kg Volume:2.54546e-006 m^3 Density:1 kg/m^3 Weight:2.49455e-005 N | C:\Users\fenobus\OneDrive - City, University of London\SolidworksFiles\fs\18650\EndCap.SLDPRT Feb 26 18:34:28 2018
Boss-Extrude4 | Solid Body | Mass:2.54546e-006 kg Volume:2.54546e-006 m^3 Density:1 kg/m^3 Weight:2.49455e-005 N | C:\Users\fenobus\OneDrive - City, University of London\SolidworksFiles\fs\18650\EndCap.SLDPRT Feb 26 18:34:28 2018
Boss-Extrude3 | Solid Body | Mass:1.70971e-005 kg Volume:1.70971e-005 m^3 Density:1 kg/m^3 Weight:0.000167551 N | C:\Users\fenobus\OneDrive - City, University of London\SolidworksFiles\fs\18650\HB2.SLDPRT Feb 25 17:30:42 2018
Boss-Extrude4 | Solid Body | Mass:2.54546e-006 kg Volume:2.54546e-006 m^3 Density:1 kg/m^3 Weight:2.49455e-005 N | C:\Users\fenobus\OneDrive - City, University of London\SolidworksFiles\fs\18650\EndCap.SLDPRT Feb 26 18:34:28 2018
Boss-Extrude4 | Solid Body | Mass:2.54546e-006 kg Volume:2.54546e-006 m^3 Density:1 kg/m^3 Weight:2.49455e-005 N | C:\Users\fenobus\OneDrive - City, University of London\SolidworksFiles\fs\18650\EndCap.SLDPRT Feb 26 18:34:28 2018
Boss-Extrude3 | Solid Body | Mass:1.70971e-005 kg Volume:1.70971e-005 m^3 Density:1 kg/m^3 Weight:0.000167551 N | C:\Users\fenobus\OneDrive - City, University of London\SolidworksFiles\fs\18650\HB2.SLDPRT Feb 25 17:30:42 2018
Boss-Extrude4 | Solid Body | Mass:2.54546e-006 kg Volume:2.54546e-006 m^3 Density:1 kg/m^3 Weight:2.49455e-005 N | C:\Users\fenobus\OneDrive - City, University of London\SolidworksFiles\fs\18650\EndCap.SLDPRT Feb 26 18:34:28 2018
Boss-Extrude4 | Solid Body | Mass:2.54546e-006 kg Volume:2.54546e-006 m^3 Density:1 kg/m^3 Weight:2.49455e-005 N | C:\Users\fenobus\OneDrive - City, University of London\SolidworksFiles\fs\18650\EndCap.SLDPRT Feb 26 18:34:28 2018
Boss-Extrude3 | Solid Body | Mass:1.70971e-005 kg Volume:1.70971e-005 m^3 Density:1 kg/m^3 Weight:0.000167551 N | C:\Users\fenobus\OneDrive - City, University of London\SolidworksFiles\fs\18650\HB2.SLDPRT Feb 25 17:30:42 2018
Boss-Extrude4 | Solid Body | Mass:2.54546e-006 kg Volume:2.54546e-006 m^3 Density:1 kg/m^3 Weight:2.49455e-005 N | C:\Users\fenobus\OneDrive - City, University of London\SolidworksFiles\fs\18650\EndCap.SLDPRT Feb 26 18:34:28 2018
Boss-Extrude4 | Solid Body | Mass:2.54546e-006 kg Volume:2.54546e-006 m^3 Density:1 kg/m^3 Weight:2.49455e-005 N | C:\Users\fenobus\OneDrive - City, University of London\SolidworksFiles\fs\18650\EndCap.SLDPRT Feb 26 18:34:28 2018
Boss-Extrude3 | Solid Body | Mass:1.70971e-005 kg Volume:1.70971e-005 m^3 Density:1 kg/m^3 Weight:0.000167551 N | C:\Users\fenobus\OneDrive - City, University of London\SolidworksFiles\fs\18650\HB2.SLDPRT Feb 25 17:30:42 2018
Boss-Extrude4 | Solid Body | Mass:2.54546e-006 kg Volume:2.54546e-006 m^3 Density:1 kg/m^3 Weight:2.49455e-005 N | C:\Users\fenobus\OneDrive - City, University of London\SolidworksFiles\fs\18650\EndCap.SLDPRT Feb 26 18:34:28 2018
Boss-Extrude4 | Solid Body | Mass:2.54546e-006 kg Volume:2.54546e-006 m^3 Density:1 kg/m^3 Weight:2.49455e-005 N | C:\Users\fenobus\OneDrive - City, University of London\SolidworksFiles\fs\18650\EndCap.SLDPRT Feb 26 18:34:28 2018
Boss-Extrude3 | Solid Body | Mass:1.70971e-005 kg Volume:1.70971e-005 m^3 Density:1 kg/m^3 Weight:0.000167551 N | C:\Users\fenobus\OneDrive - City, University of London\SolidworksFiles\fs\18650\HB2.SLDPRT Feb 25 17:30:42 2018
Boss-Extrude4 | Solid Body | Mass:2.54546e-006 kg Volume:2.54546e-006 m^3 Density:1 kg/m^3 Weight:2.49455e-005 N | C:\Users\fenobus\OneDrive - City, University of London\SolidworksFiles\fs\18650\EndCap.SLDPRT Feb 26 18:34:28 2018
Boss-Extrude4 | Solid Body | Mass:2.54546e-006 kg Volume:2.54546e-006 m^3 Density:1 kg/m^3 Weight:2.49455e-005 N | C:\Users\fenobus\OneDrive - City, University of London\SolidworksFiles\fs\18650\EndCap.SLDPRT Feb 26 18:34:28 2018
Boss-Extrude3 | Solid Body | Mass:1.70971e-005 kg Volume:1.70971e-005 m^3 Density:1 kg/m^3 Weight:0.000167551 N | C:\Users\fenobus\OneDrive - City, University of London\SolidworksFiles\fs\18650\HB2.SLDPRT Feb 25 17:30:42 2018
Boss-Extrude4 | Solid Body | Mass:2.54546e-006 kg Volume:2.54546e-006 m^3 Density:1 kg/m^3 Weight:2.49455e-005 N | C:\Users\fenobus\OneDrive - City, University of London\SolidworksFiles\fs\18650\EndCap.SLDPRT Feb 26 18:34:28 2018
Boss-Extrude4 | Solid Body | Mass:2.54546e-006 kg Volume:2.54546e-006 m^3 Density:1 kg/m^3 Weight:2.49455e-005 N | C:\Users\fenobus\OneDrive - City, University of London\SolidworksFiles\fs\18650\EndCap.SLDPRT Feb 26 18:34:28 2018
Boss-Extrude3 | Solid Body | Mass:1.70971e-005 kg Volume:1.70971e-005 m^3 Density:1 kg/m^3 Weight:0.000167551 N | C:\Users\fenobus\OneDrive - City, University of London\SolidworksFiles\fs\18650\HB2.SLDPRT Feb 25 17:30:42 2018
Boss-Extrude4 | Solid Body | Mass:2.54546e-006 kg Volume:2.54546e-006 m^3 Density:1 kg/m^3 Weight:2.49455e-005 N | C:\Users\fenobus\OneDrive - City, University of London\SolidworksFiles\fs\18650\EndCap.SLDPRT Feb 26 18:34:28 2018
Boss-Extrude4 | Solid Body | Mass:2.54546e-006 kg Volume:2.54546e-006 m^3 Density:1 kg/m^3 Weight:2.49455e-005 N | C:\Users\fenobus\OneDrive - City, University of London\SolidworksFiles\fs\18650\EndCap.SLDPRT Feb 26 18:34:28 2018
Boss-Extrude3 | Solid Body | Mass:1.70971e-005 kg Volume:1.70971e-005 m^3 Density:1 kg/m^3 Weight:0.000167551 N | C:\Users\fenobus\OneDrive - City, University of London\SolidworksFiles\fs\18650\HB2.SLDPRT Feb 25 17:30:42 2018
Boss-Extrude4 | Solid Body | Mass:2.54546e-006 kg Volume:2.54546e-006 m^3 Density:1 kg/m^3 Weight:2.49455e-005 N | C:\Users\fenobus\OneDrive - City, University of London\SolidworksFiles\fs\18650\EndCap.SLDPRT Feb 26 18:34:28 2018
Boss-Extrude4 | Solid Body | Mass:2.54546e-006 kg Volume:2.54546e-006 m^3 Density:1 kg/m^3 Weight:2.49455e-005 N | C:\Users\fenobus\OneDrive - City, University of London\SolidworksFiles\fs\18650\EndCap.SLDPRT Feb 26 18:34:28 2018
Boss-Extrude3 | Solid Body | Mass:1.70971e-005 kg Volume:1.70971e-005 m^3 Density:1 kg/m^3 Weight:0.000167551 N | C:\Users\fenobus\OneDrive - City, University of London\SolidworksFiles\fs\18650\HB2.SLDPRT Feb 25 17:30:42 2018
Boss-Extrude4 | Solid Body | Mass:2.54546e-006 kg Volume:2.54546e-006 m^3 Density:1 kg/m^3 Weight:2.49455e-005 N | C:\Users\fenobus\OneDrive - City, University of London\SolidworksFiles\fs\18650\EndCap.SLDPRT Feb 26 18:34:28 2018
Boss-Extrude4 | Solid Body | Mass:2.54546e-006 kg Volume:2.54546e-006 m^3 Density:1 kg/m^3 Weight:2.49455e-005 N | C:\Users\fenobus\OneDrive - City, University of London\SolidworksFiles\fs\18650\EndCap.SLDPRT Feb 26 18:34:28 2018
Boss-Extrude3 | Solid Body | Mass:1.70971e-005 kg Volume:1.70971e-005 m^3 Density:1 kg/m^3 Weight:0.000167551 N | C:\Users\fenobus\OneDrive - City, University of London\SolidworksFiles\fs\18650\HB2.SLDPRT Feb 25 17:30:42 2018
Boss-Extrude4 | Solid Body | Mass:2.54546e-006 kg Volume:2.54546e-006 m^3 Density:1 kg/m^3 Weight:2.49455e-005 N | C:\Users\fenobus\OneDrive - City, University of London\SolidworksFiles\fs\18650\EndCap.SLDPRT Feb 26 18:34:28 2018
Boss-Extrude4 | Solid Body | Mass:2.54546e-006 kg Volume:2.54546e-006 m^3 Density:1 kg/m^3 Weight:2.49455e-005 N | C:\Users\fenobus\OneDrive - City, University of London\SolidworksFiles\fs\18650\EndCap.SLDPRT Feb 26 18:34:28 2018
Boss-Extrude3 | Solid Body | Mass:1.70971e-005 kg Volume:1.70971e-005 m^3 Density:1 kg/m^3 Weight:0.000167551 N | C:\Users\fenobus\OneDrive - City, University of London\SolidworksFiles\fs\18650\HB2.SLDPRT Feb 25 17:30:42 2018
Boss-Extrude4 | Solid Body | Mass:2.54546e-006 kg Volume:2.54546e-006 m^3 Density:1 kg/m^3 Weight:2.49455e-005 N | C:\Users\fenobus\OneDrive - City, University of London\SolidworksFiles\fs\18650\EndCap.SLDPRT Feb 26 18:34:28 2018
Boss-Extrude4 | Solid Body | Mass:2.54546e-006 kg Volume:2.54546e-006 m^3 Density:1 kg/m^3 Weight:2.49455e-005 N | C:\Users\fenobus\OneDrive - City, University of London\SolidworksFiles\fs\18650\EndCap.SLDPRT Feb 26 18:34:28 2018
Boss-Extrude3 | Solid Body | Mass:1.70971e-005 kg Volume:1.70971e-005 m^3 Density:1 kg/m^3 Weight:0.000167551 N | C:\Users\fenobus\OneDrive - City, University of London\SolidworksFiles\fs\18650\HB2.SLDPRT Feb 25 17:30:42 2018
Boss-Extrude4 | Solid Body | Mass:2.54546e-006 kg Volume:2.54546e-006 m^3 Density:1 kg/m^3 Weight:2.49455e-005 N | C:\Users\fenobus\OneDrive - City, University of London\SolidworksFiles\fs\18650\EndCap.SLDPRT Feb 26 18:34:28 2018
Boss-Extrude4 | Solid Body | Mass:2.54546e-006 kg Volume:2.54546e-006 m^3 Density:1 kg/m^3 Weight:2.49455e-005 N | C:\Users\fenobus\OneDrive - City, University of London\SolidworksFiles\fs\18650\EndCap.SLDPRT Feb 26 18:34:28 2018
Boss-Extrude3 | Solid Body | Mass:1.70971e-005 kg Volume:1.70971e-005 m^3 Density:1 kg/m^3 Weight:0.000167551 N | C:\Users\fenobus\OneDrive - City, University of London\SolidworksFiles\fs\18650\HB2.SLDPRT Feb 25 17:30:42 2018
Boss-Extrude4 | Solid Body | Mass:2.54546e-006 kg Volume:2.54546e-006 m^3 Density:1 kg/m^3 Weight:2.49455e-005 N | C:\Users\fenobus\OneDrive - City, University of London\SolidworksFiles\fs\18650\EndCap.SLDPRT Feb 26 18:34:28 2018
Boss-Extrude4 | Solid Body | Mass:2.54546e-006 kg Volume:2.54546e-006 m^3 Density:1 kg/m^3 Weight:2.49455e-005 N | C:\Users\fenobus\OneDrive - City, University of London\SolidworksFiles\fs\18650\EndCap.SLDPRT Feb 26 18:34:28 2018
Boss-Extrude3 | Solid Body | Mass:1.70971e-005 kg Volume:1.70971e-005 m^3 Density:1 kg/m^3 Weight:0.000167551 N | C:\Users\fenobus\OneDrive - City, University of London\SolidworksFiles\fs\18650\HB2.SLDPRT Feb 25 17:30:42 2018
Boss-Extrude4 | Solid Body | Mass:2.54546e-006 kg Volume:2.54546e-006 m^3 Density:1 kg/m^3 Weight:2.49455e-005 N | C:\Users\fenobus\OneDrive - City, University of London\SolidworksFiles\fs\18650\EndCap.SLDPRT Feb 26 18:34:28 2018
Boss-Extrude4 | Solid Body | Mass:2.54546e-006 kg Volume:2.54546e-006 m^3 Density:1 kg/m^3 Weight:2.49455e-005 N | C:\Users\fenobus\OneDrive - City, University of London\SolidworksFiles\fs\18650\EndCap.SLDPRT Feb 26 18:34:28 2018
Boss-Extrude3 | Solid Body | Mass:1.70971e-005 kg Volume:1.70971e-005 m^3 Density:1 kg/m^3 Weight:0.000167551 N | C:\Users\fenobus\OneDrive - City, University of London\SolidworksFiles\fs\18650\HB2.SLDPRT Feb 25 17:30:42 2018
Boss-Extrude4 | Solid Body | Mass:2.54546e-006 kg Volume:2.54546e-006 m^3 Density:1 kg/m^3 Weight:2.49455e-005 N | C:\Users\fenobus\OneDrive - City, University of London\SolidworksFiles\fs\18650\EndCap.SLDPRT Feb 26 18:34:28 2018
Boss-Extrude4 | Solid Body | Mass:2.54546e-006 kg Volume:2.54546e-006 m^3 Density:1 kg/m^3 Weight:2.49455e-005 N | C:\Users\fenobus\OneDrive - City, University of London\SolidworksFiles\fs\18650\EndCap.SLDPRT Feb 26 18:34:28 2018
Boss-Extrude3 | Solid Body | Mass:1.70971e-005 kg Volume:1.70971e-005 m^3 Density:1 kg/m^3 Weight:0.000167551 N | C:\Users\fenobus\OneDrive - City, University of London\SolidworksFiles\fs\18650\HB2.SLDPRT Feb 25 17:30:42 2018
Boss-Extrude4 | Solid Body | Mass:2.54546e-006 kg Volume:2.54546e-006 m^3 Density:1 kg/m^3 Weight:2.49455e-005 N | C:\Users\fenobus\OneDrive - City, University of London\SolidworksFiles\fs\18650\EndCap.SLDPRT Feb 26 18:34:28 2018
Boss-Extrude4 | Solid Body | Mass:2.54546e-006 kg Volume:2.54546e-006 m^3 Density:1 kg/m^3 Weight:2.49455e-005 N | C:\Users\fenobus\OneDrive - City, University of London\SolidworksFiles\fs\18650\EndCap.SLDPRT Feb 26 18:34:28 2018
Boss-Extrude3 | Solid Body | Mass:1.70971e-005 kg Volume:1.70971e-005 m^3 Density:1 kg/m^3 Weight:0.000167551 N | C:\Users\fenobus\OneDrive - City, University of London\SolidworksFiles\fs\18650\HB2.SLDPRT Feb 25 17:30:42 2018
Boss-Extrude4 | Solid Body | Mass:2.54546e-006 kg Volume:2.54546e-006 m^3 Density:1 kg/m^3 Weight:2.49455e-005 N | C:\Users\fenobus\OneDrive - City, University of London\SolidworksFiles\fs\18650\EndCap.SLDPRT Feb 26 18:34:28 2018
Boss-Extrude4 | Solid Body | Mass:2.54546e-006 kg Volume:2.54546e-006 m^3 Density:1 kg/m^3 Weight:2.49455e-005 N | C:\Users\fenobus\OneDrive - City, University of London\SolidworksFiles\fs\18650\EndCap.SLDPRT Feb 26 18:34:28 2018
Boss-Extrude3 | Solid Body | Mass:1.70971e-005 kg Volume:1.70971e-005 m^3 Density:1 kg/m^3 Weight:0.000167551 N | C:\Users\fenobus\OneDrive - City, University of London\SolidworksFiles\fs\18650\HB2.SLDPRT Feb 25 17:30:42 2018
Boss-Extrude4 | Solid Body | Mass:2.54546e-006 kg Volume:2.54546e-006 m^3 Density:1 kg/m^3 Weight:2.49455e-005 N | C:\Users\fenobus\OneDrive - City, University of London\SolidworksFiles\fs\18650\EndCap.SLDPRT Feb 26 18:34:28 2018
Boss-Extrude4 | Solid Body | Mass:2.54546e-006 kg Volume:2.54546e-006 m^3 Density:1 kg/m^3 Weight:2.49455e-005 N | C:\Users\fenobus\OneDrive - City, University of London\SolidworksFiles\fs\18650\EndCap.SLDPRT Feb 26 18:34:28 2018
Boss-Extrude3 | Solid Body | Mass:1.70971e-005 kg Volume:1.70971e-005 m^3 Density:1 kg/m^3 Weight:0.000167551 N | C:\Users\fenobus\OneDrive - City, University of London\SolidworksFiles\fs\18650\HB2.SLDPRT Feb 25 17:30:42 2018
Boss-Extrude4 | Solid Body | Mass:2.54546e-006 kg Volume:2.54546e-006 m^3 Density:1 kg/m^3 Weight:2.49455e-005 N | C:\Users\fenobus\OneDrive - City, University of London\SolidworksFiles\fs\18650\EndCap.SLDPRT Feb 26 18:34:28 2018
Boss-Extrude4 | Solid Body | Mass:2.54546e-006 kg Volume:2.54546e-006 m^3 Density:1 kg/m^3 Weight:2.49455e-005 N | C:\Users\fenobus\OneDrive - City, University of London\SolidworksFiles\fs\18650\EndCap.SLDPRT Feb 26 18:34:28 2018
Boss-Extrude3 | Solid Body | Mass:1.70971e-005 kg Volume:1.70971e-005 m^3 Density:1 kg/m^3 Weight:0.000167551 N | C:\Users\fenobus\OneDrive - City, University of London\SolidworksFiles\fs\18650\HB2.SLDPRT Feb 25 17:30:42 2018
Boss-Extrude4 | Solid Body | Mass:2.54546e-006 kg Volume:2.54546e-006 m^3 Density:1 kg/m^3 Weight:2.49455e-005 N | C:\Users\fenobus\OneDrive - City, University of London\SolidworksFiles\fs\18650\EndCap.SLDPRT Feb 26 18:34:28 2018
Boss-Extrude4 | Solid Body | Mass:2.54546e-006 kg Volume:2.54546e-006 m^3 Density:1 kg/m^3 Weight:2.49455e-005 N | C:\Users\fenobus\OneDrive - City, University of London\SolidworksFiles\fs\18650\EndCap.SLDPRT Feb 26 18:34:28 2018
Boss-Extrude3 | Solid Body | Mass:1.70971e-005 kg Volume:1.70971e-005 m^3 Density:1 kg/m^3 Weight:0.000167551 N | C:\Users\fenobus\OneDrive - City, University of London\SolidworksFiles\fs\18650\HB2.SLDPRT Feb 25 17:30:42 2018
Boss-Extrude4 | Solid Body | Mass:2.54546e-006 kg Volume:2.54546e-006 m^3 Density:1 kg/m^3 Weight:2.49455e-005 N | C:\Users\fenobus\OneDrive - City, University of London\SolidworksFiles\fs\18650\EndCap.SLDPRT Feb 26 18:34:28 2018
Boss-Extrude4 | Solid Body | Mass:2.54546e-006 kg Volume:2.54546e-006 m^3 Density:1 kg/m^3 Weight:2.49455e-005 N | C:\Users\fenobus\OneDrive - City, University of London\SolidworksFiles\fs\18650\EndCap.SLDPRT Feb 26 18:34:28 2018
Boss-Extrude3 | Solid Body | Mass:1.70971e-005 kg Volume:1.70971e-005 m^3 Density:1 kg/m^3 Weight:0.000167551 N | C:\Users\fenobus\OneDrive - City, University of London\SolidworksFiles\fs\18650\HB2.SLDPRT Feb 25 17:30:42 2018
Boss-Extrude4 | Solid Body | Mass:2.54546e-006 kg Volume:2.54546e-006 m^3 Density:1 kg/m^3 Weight:2.49455e-005 N | C:\Users\fenobus\OneDrive - City, University of London\SolidworksFiles\fs\18650\EndCap.SLDPRT Feb 26 18:34:28 2018
Boss-Extrude4 | Solid Body | Mass:2.54546e-006 kg Volume:2.54546e-006 m^3 Density:1 kg/m^3 Weight:2.49455e-005 N | C:\Users\fenobus\OneDrive - City, University of London\SolidworksFiles\fs\18650\EndCap.SLDPRT Feb 26 18:34:28 2018
Boss-Extrude3 | Solid Body | Mass:1.70971e-005 kg Volume:1.70971e-005 m^3 Density:1 kg/m^3 Weight:0.000167551 N | C:\Users\fenobus\OneDrive - City, University of London\SolidworksFiles\fs\18650\HB2.SLDPRT Feb 25 17:30:42 2018
Boss-Extrude4 | Solid Body | Mass:2.54546e-006 kg Volume:2.54546e-006 m^3 Density:1 kg/m^3 Weight:2.49455e-005 N | C:\Users\fenobus\OneDrive - City, University of London\SolidworksFiles\fs\18650\EndCap.SLDPRT Feb 26 18:34:28 2018
Boss-Extrude4 | Solid Body | Mass:2.54546e-006 kg Volume:2.54546e-006 m^3 Density:1 kg/m^3 Weight:2.49455e-005 N | C:\Users\fenobus\OneDrive - City, University of London\SolidworksFiles\fs\18650\EndCap.SLDPRT Feb 26 18:34:28 2018
Boss-Extrude3 | Solid Body | Mass:1.70971e-005 kg Volume:1.70971e-005 m^3 Density:1 kg/m^3 Weight:0.000167551 N | C:\Users\fenobus\OneDrive - City, University of London\SolidworksFiles\fs\18650\HB2.SLDPRT Feb 25 17:30:42 2018
Boss-Extrude4 | Solid Body | Mass:2.54546e-006 kg Volume:2.54546e-006 m^3 Density:1 kg/m^3 Weight:2.49455e-005 N | C:\Users\fenobus\OneDrive - City, University of London\SolidworksFiles\fs\18650\EndCap.SLDPRT Feb 26 18:34:28 2018
Boss-Extrude4 | Solid Body | Mass:2.54546e-006 kg Volume:2.54546e-006 m^3 Density:1 kg/m^3 Weight:2.49455e-005 N | C:\Users\fenobus\OneDrive - City, University of London\SolidworksFiles\fs\18650\EndCap.SLDPRT Feb 26 18:34:28 2018
Boss-Extrude3 | Solid Body | Mass:1.70971e-005 kg Volume:1.70971e-005 m^3 Density:1 kg/m^3 Weight:0.000167551 N | C:\Users\fenobus\OneDrive - City, University of London\SolidworksFiles\fs\18650\HB2.SLDPRT Feb 25 17:30:42 2018
Boss-Extrude4 | Solid Body | Mass:2.54546e-006 kg Volume:2.54546e-006 m^3 Density:1 kg/m^3 Weight:2.49455e-005 N | C:\Users\fenobus\OneDrive - City, University of London\SolidworksFiles\fs\18650\EndCap.SLDPRT Feb 26 18:34:28 2018
Boss-Extrude4 | Solid Body | Mass:2.54546e-006 kg Volume:2.54546e-006 m^3 Density:1 kg/m^3 Weight:2.49455e-005 N | C:\Users\fenobus\OneDrive - City, University of London\SolidworksFiles\fs\18650\EndCap.SLDPRT Feb 26 18:34:28 2018
Boss-Extrude3 | Solid Body | Mass:1.70971e-005 kg Volume:1.70971e-005 m^3 Density:1 kg/m^3 Weight:0.000167551 N | C:\Users\fenobus\OneDrive - City, University of London\SolidworksFiles\fs\18650\HB2.SLDPRT Feb 25 17:30:42 2018
Boss-Extrude4 | Solid Body | Mass:2.54546e-006 kg Volume:2.54546e-006 m^3 Density:1 kg/m^3 Weight:2.49455e-005 N | C:\Users\fenobus\OneDrive - City, University of London\SolidworksFiles\fs\18650\EndCap.SLDPRT Feb 26 18:34:28 2018
Boss-Extrude4 | Solid Body | Mass:2.54546e-006 kg Volume:2.54546e-006 m^3 Density:1 kg/m^3 Weight:2.49455e-005 N | C:\Users\fenobus\OneDrive - City, University of London\SolidworksFiles\fs\18650\EndCap.SLDPRT Feb 26 18:34:28 2018
Boss-Extrude3 | Solid Body | Mass:1.70971e-005 kg Volume:1.70971e-005 m^3 Density:1 kg/m^3 Weight:0.000167551 N | C:\Users\fenobus\OneDrive - City, University of London\SolidworksFiles\fs\18650\HB2.SLDPRT Feb 25 17:30:42 2018
Boss-Extrude4 | Solid Body | Mass:2.54546e-006 kg Volume:2.54546e-006 m^3 Density:1 kg/m^3 Weight:2.49455e-005 N | C:\Users\fenobus\OneDrive - City, University of London\SolidworksFiles\fs\18650\EndCap.SLDPRT Feb 26 18:34:28 2018
Boss-Extrude4 | Solid Body | Mass:2.54546e-006 kg Volume:2.54546e-006 m^3 Density:1 kg/m^3 Weight:2.49455e-005 N | C:\Users\fenobus\OneDrive - City, University of London\SolidworksFiles\fs\18650\EndCap.SLDPRT Feb 26 18:34:28 2018
Boss-Extrude3 | Solid Body | Mass:1.70971e-005 kg Volume:1.70971e-005 m^3 Density:1 kg/m^3 Weight:0.000167551 N | C:\Users\fenobus\OneDrive - City, University of London\SolidworksFiles\fs\18650\HB2.SLDPRT Feb 25 17:30:42 2018
Boss-Extrude4 | Solid Body | Mass:2.54546e-006 kg Volume:2.54546e-006 m^3 Density:1 kg/m^3 Weight:2.49455e-005 N | C:\Users\fenobus\OneDrive - City, University of London\SolidworksFiles\fs\18650\EndCap.SLDPRT Feb 26 18:34:28 2018
Boss-Extrude4 | Solid Body | Mass:2.54546e-006 kg Volume:2.54546e-006 m^3 Density:1 kg/m^3 Weight:2.49455e-005 N | C:\Users\fenobus\OneDrive - City, University of London\SolidworksFiles\fs\18650\EndCap.SLDPRT Feb 26 18:34:28 2018
Boss-Extrude3 | Solid Body | Mass:1.70971e-005 kg Volume:1.70971e-005 m^3 Density:1 kg/m^3 Weight:0.000167551 N | C:\Users\fenobus\OneDrive - City, University of London\SolidworksFiles\fs\18650\HB2.SLDPRT Feb 25 17:30:42 2018
Boss-Extrude4 | Solid Body | Mass:2.54546e-006 kg Volume:2.54546e-006 m^3 Density:1 kg/m^3 Weight:2.49455e-005 N | C:\Users\fenobus\OneDrive - City, University of London\SolidworksFiles\fs\18650\EndCap.SLDPRT Feb 26 18:34:28 2018
Boss-Extrude4 | Solid Body | Mass:2.54546e-006 kg Volume:2.54546e-006 m^3 Density:1 kg/m^3 Weight:2.49455e-005 N | C:\Users\fenobus\OneDrive - City, University of London\SolidworksFiles\fs\18650\EndCap.SLDPRT Feb 26 18:34:28 2018
Boss-Extrude3 | Solid Body | Mass:1.70971e-005 kg Volume:1.70971e-005 m^3 Density:1 kg/m^3 Weight:0.000167551 N | C:\Users\fenobus\OneDrive - City, University of London\SolidworksFiles\fs\18650\HB2.SLDPRT Feb 25 17:30:42 2018
Boss-Extrude4 | Solid Body | Mass:2.54546e-006 kg Volume:2.54546e-006 m^3 Density:1 kg/m^3 Weight:2.49455e-005 N | C:\Users\fenobus\OneDrive - City, University of London\SolidworksFiles\fs\18650\EndCap.SLDPRT Feb 26 18:34:28 2018
Boss-Extrude4 | Solid Body | Mass:2.54546e-006 kg Volume:2.54546e-006 m^3 Density:1 kg/m^3 Weight:2.49455e-005 N | C:\Users\fenobus\OneDrive - City, University of London\SolidworksFiles\fs\18650\EndCap.SLDPRT Feb 26 18:34:28 2018
Boss-Extrude3 | Solid Body | Mass:1.70971e-005 kg Volume:1.70971e-005 m^3 Density:1 kg/m^3 Weight:0.000167551 N | C:\Users\fenobus\OneDrive - City, University of London\SolidworksFiles\fs\18650\HB2.SLDPRT Feb 25 17:30:42 2018
Boss-Extrude4 | Solid Body | Mass:2.54546e-006 kg Volume:2.54546e-006 m^3 Density:1 kg/m^3 Weight:2.49455e-005 N | C:\Users\fenobus\OneDrive - City, University of London\SolidworksFiles\fs\18650\EndCap.SLDPRT Feb 26 18:34:28 2018
Boss-Extrude4 | Solid Body | Mass:2.54546e-006 kg Volume:2.54546e-006 m^3 Density:1 kg/m^3 Weight:2.49455e-005 N | C:\Users\fenobus\OneDrive - City, University of London\SolidworksFiles\fs\18650\EndCap.SLDPRT Feb 26 18:34:28 2018
Boss-Extrude3 | Solid Body | Mass:1.70971e-005 kg Volume:1.70971e-005 m^3 Density:1 kg/m^3 Weight:0.000167551 N | C:\Users\fenobus\OneDrive - City, University of London\SolidworksFiles\fs\18650\HB2.SLDPRT Feb 25 17:30:42 2018
Boss-Extrude4 | Solid Body | Mass:2.54546e-006 kg Volume:2.54546e-006 m^3 Density:1 kg/m^3 Weight:2.49455e-005 N | C:\Users\fenobus\OneDrive - City, University of London\SolidworksFiles\fs\18650\EndCap.SLDPRT Feb 26 18:34:28 2018
Boss-Extrude4 | Solid Body | Mass:2.54546e-006 kg Volume:2.54546e-006 m^3 Density:1 kg/m^3 Weight:2.49455e-005 N | C:\Users\fenobus\OneDrive - City, University of London\SolidworksFiles\fs\18650\EndCap.SLDPRT Feb 26 18:34:28 2018
Boss-Extrude3 | Solid Body | Mass:1.70971e-005 kg Volume:1.70971e-005 m^3 Density:1 kg/m^3 Weight:0.000167551 N | C:\Users\fenobus\OneDrive - City, University of London\SolidworksFiles\fs\18650\HB2.SLDPRT Feb 25 17:30:42 2018
Boss-Extrude4 | Solid Body | Mass:2.54546e-006 kg Volume:2.54546e-006 m^3 Density:1 kg/m^3 Weight:2.49455e-005 N | C:\Users\fenobus\OneDrive - City, University of London\SolidworksFiles\fs\18650\EndCap.SLDPRT Feb 26 18:34:28 2018
Boss-Extrude4 | Solid Body | Mass:2.54546e-006 kg Volume:2.54546e-006 m^3 Density:1 kg/m^3 Weight:2.49455e-005 N | C:\Users\fenobus\OneDrive - City, University of London\SolidworksFiles\fs\18650\EndCap.SLDPRT Feb 26 18:34:28 2018
Boss-Extrude3 | Solid Body | Mass:1.70971e-005 kg Volume:1.70971e-005 m^3 Density:1 kg/m^3 Weight:0.000167551 N | C:\Users\fenobus\OneDrive - City, University of London\SolidworksFiles\fs\18650\HB2.SLDPRT Feb 25 17:30:42 2018
Boss-Extrude4 | Solid Body | Mass:2.54546e-006 kg Volume:2.54546e-006 m^3 Density:1 kg/m^3 Weight:2.49455e-005 N | C:\Users\fenobus\OneDrive - City, University of London\SolidworksFiles\fs\18650\EndCap.SLDPRT Feb 26 18:34:28 2018
Boss-Extrude4 | Solid Body | Mass:2.54546e-006 kg Volume:2.54546e-006 m^3 Density:1 kg/m^3 Weight:2.49455e-005 N | C:\Users\fenobus\OneDrive - City, University of London\SolidworksFiles\fs\18650\EndCap.SLDPRT Feb 26 18:34:28 2018
Boss-Extrude3 | Solid Body | Mass:1.70971e-005 kg Volume:1.70971e-005 m^3 Density:1 kg/m^3 Weight:0.000167551 N | C:\Users\fenobus\OneDrive - City, University of London\SolidworksFiles\fs\18650\HB2.SLDPRT Feb 25 17:30:42 2018
Boss-Extrude4 | Solid Body | Mass:2.54546e-006 kg Volume:2.54546e-006 m^3 Density:1 kg/m^3 Weight:2.49455e-005 N | C:\Users\fenobus\OneDrive - City, University of London\SolidworksFiles\fs\18650\EndCap.SLDPRT Feb 26 18:34:28 2018
Boss-Extrude4 | Solid Body | Mass:2.54546e-006 kg Volume:2.54546e-006 m^3 Density:1 kg/m^3 Weight:2.49455e-005 N | C:\Users\fenobus\OneDrive - City, University of London\SolidworksFiles\fs\18650\EndCap.SLDPRT Feb 26 18:34:28 2018
Boss-Extrude3 | Solid Body | Mass:1.70971e-005 kg Volume:1.70971e-005 m^3 Density:1 kg/m^3 Weight:0.000167551 N | C:\Users\fenobus\OneDrive - City, University of London\SolidworksFiles\fs\18650\HB2.SLDPRT Feb 25 17:30:42 2018
Boss-Extrude4 | Solid Body | Mass:2.54546e-006 kg Volume:2.54546e-006 m^3 Density:1 kg/m^3 Weight:2.49455e-005 N | C:\Users\fenobus\OneDrive - City, University of London\SolidworksFiles\fs\18650\EndCap.SLDPRT Feb 26 18:34:28 2018
Boss-Extrude4 | Solid Body | Mass:2.54546e-006 kg Volume:2.54546e-006 m^3 Density:1 kg/m^3 Weight:2.49455e-005 N | C:\Users\fenobus\OneDrive - City, University of London\SolidworksFiles\fs\18650\EndCap.SLDPRT Feb 26 18:34:28 2018
Boss-Extrude3 | Solid Body | Mass:1.70971e-005 kg Volume:1.70971e-005 m^3 Density:1 kg/m^3 Weight:0.000167551 N | C:\Users\fenobus\OneDrive - City, University of London\SolidworksFiles\fs\18650\HB2.SLDPRT Feb 25 17:30:42 2018
Boss-Extrude4 | Solid Body | Mass:2.54546e-006 kg Volume:2.54546e-006 m^3 Density:1 kg/m^3 Weight:2.49455e-005 N | C:\Users\fenobus\OneDrive - City, University of London\SolidworksFiles\fs\18650\EndCap.SLDPRT Feb 26 18:34:28 2018
Boss-Extrude4 | Solid Body | Mass:2.54546e-006 kg Volume:2.54546e-006 m^3 Density:1 kg/m^3 Weight:2.49455e-005 N | C:\Users\fenobus\OneDrive - City, University of London\SolidworksFiles\fs\18650\EndCap.SLDPRT Feb 26 18:34:28 2018
Boss-Extrude3 | Solid Body | Mass:1.70971e-005 kg Volume:1.70971e-005 m^3 Density:1 kg/m^3 Weight:0.000167551 N | C:\Users\fenobus\OneDrive - City, University of London\SolidworksFiles\fs\18650\HB2.SLDPRT Feb 25 17:30:42 2018
Boss-Extrude4 | Solid Body | Mass:2.54546e-006 kg Volume:2.54546e-006 m^3 Density:1 kg/m^3 Weight:2.49455e-005 N | C:\Users\fenobus\OneDrive - City, University of London\SolidworksFiles\fs\18650\EndCap.SLDPRT Feb 26 18:34:28 2018
Boss-Extrude4 | Solid Body | Mass:2.54546e-006 kg Volume:2.54546e-006 m^3 Density:1 kg/m^3 Weight:2.49455e-005 N | C:\Users\fenobus\OneDrive - City, University of London\SolidworksFiles\fs\18650\EndCap.SLDPRT Feb 26 18:34:28 2018
Boss-Extrude3 | Solid Body | Mass:1.70971e-005 kg Volume:1.70971e-005 m^3 Density:1 kg/m^3 Weight:0.000167551 N | C:\Users\fenobus\OneDrive - City, University of London\SolidworksFiles\fs\18650\HB2.SLDPRT Feb 25 17:30:42 2018
Boss-Extrude4 | Solid Body | Mass:2.54546e-006 kg Volume:2.54546e-006 m^3 Density:1 kg/m^3 Weight:2.49455e-005 N | C:\Users\fenobus\OneDrive - City, University of London\SolidworksFiles\fs\18650\EndCap.SLDPRT Feb 26 18:34:28 2018
Boss-Extrude4 | Solid Body | Mass:2.54546e-006 kg Volume:2.54546e-006 m^3 Density:1 kg/m^3 Weight:2.49455e-005 N | C:\Users\fenobus\OneDrive - City, University of London\SolidworksFiles\fs\18650\EndCap.SLDPRT Feb 26 18:34:28 2018
Boss-Extrude3 | Solid Body | Mass:1.70971e-005 kg Volume:1.70971e-005 m^3 Density:1 kg/m^3 Weight:0.000167551 N | C:\Users\fenobus\OneDrive - City, University of London\SolidworksFiles\fs\18650\HB2.SLDPRT Feb 25 17:30:42 2018
Boss-Extrude4 | Solid Body | Mass:2.54546e-006 kg Volume:2.54546e-006 m^3 Density:1 kg/m^3 Weight:2.49455e-005 N | C:\Users\fenobus\OneDrive - City, University of London\SolidworksFiles\fs\18650\EndCap.SLDPRT Feb 26 18:34:28 2018
Boss-Extrude4 | Solid Body | Mass:2.54546e-006 kg Volume:2.54546e-006 m^3 Density:1 kg/m^3 Weight:2.49455e-005 N | C:\Users\fenobus\OneDrive - City, University of London\SolidworksFiles\fs\18650\EndCap.SLDPRT Feb 26 18:34:28 2018
Boss-Extrude3 | Solid Body | Mass:1.70971e-005 kg Volume:1.70971e-005 m^3 Density:1 kg/m^3 Weight:0.000167551 N | C:\Users\fenobus\OneDrive - City, University of London\SolidworksFiles\fs\18650\HB2.SLDPRT Feb 25 17:30:42 2018
Boss-Extrude4 | Solid Body | Mass:2.54546e-006 kg Volume:2.54546e-006 m^3 Density:1 kg/m^3 Weight:2.49455e-005 N | C:\Users\fenobus\OneDrive - City, University of London\SolidworksFiles\fs\18650\EndCap.SLDPRT Feb 26 18:34:28 2018
Boss-Extrude4 | Solid Body | Mass:2.54546e-006 kg Volume:2.54546e-006 m^3 Density:1 kg/m^3 Weight:2.49455e-005 N | C:\Users\fenobus\OneDrive - City, University of London\SolidworksFiles\fs\18650\EndCap.SLDPRT Feb 26 18:34:28 2018
Boss-Extrude3 | Solid Body | Mass:1.70971e-005 kg Volume:1.70971e-005 m^3 Density:1 kg/m^3 Weight:0.000167551 N | C:\Users\fenobus\OneDrive - City, University of London\SolidworksFiles\fs\18650\HB2.SLDPRT Feb 25 17:30:42 2018
Boss-Extrude4 | Solid Body | Mass:2.54546e-006 kg Volume:2.54546e-006 m^3 Density:1 kg/m^3 Weight:2.49455e-005 N | C:\Users\fenobus\OneDrive - City, University of London\SolidworksFiles\fs\18650\EndCap.SLDPRT Feb 26 18:34:28 2018
Boss-Extrude4 | Solid Body | Mass:2.54546e-006 kg Volume:2.54546e-006 m^3 Density:1 kg/m^3 Weight:2.49455e-005 N | C:\Users\fenobus\OneDrive - City, University of London\SolidworksFiles\fs\18650\EndCap.SLDPRT Feb 26 18:34:28 2018
Boss-Extrude3 | Solid Body | Mass:1.70971e-005 kg Volume:1.70971e-005 m^3 Density:1 kg/m^3 Weight:0.000167551 N | C:\Users\fenobus\OneDrive - City, University of London\SolidworksFiles\fs\18650\HB2.SLDPRT Feb 25 17:30:42 2018
Boss-Extrude4 | Solid Body | Mass:2.54546e-006 kg Volume:2.54546e-006 m^3 Density:1 kg/m^3 Weight:2.49455e-005 N | C:\Users\fenobus\OneDrive - City, University of London\SolidworksFiles\fs\18650\EndCap.SLDPRT Feb 26 18:34:28 2018
Boss-Extrude4 | Solid Body | Mass:2.54546e-006 kg Volume:2.54546e-006 m^3 Density:1 kg/m^3 Weight:2.49455e-005 N | C:\Users\fenobus\OneDrive - City, University of London\SolidworksFiles\fs\18650\EndCap.SLDPRT Feb 26 18:34:28 2018
Boss-Extrude3 | Solid Body | Mass:1.70971e-005 kg Volume:1.70971e-005 m^3 Density:1 kg/m^3 Weight:0.000167551 N | C:\Users\fenobus\OneDrive - City, University of London\SolidworksFiles\fs\18650\HB2.SLDPRT Feb 25 17:30:42 2018
Boss-Extrude4 | Solid Body | Mass:2.54546e-006 kg Volume:2.54546e-006 m^3 Density:1 kg/m^3 Weight:2.49455e-005 N | C:\Users\fenobus\OneDrive - City, University of London\SolidworksFiles\fs\18650\EndCap.SLDPRT Feb 26 18:34:28 2018
Boss-Extrude4 | Solid Body | Mass:2.54546e-006 kg Volume:2.54546e-006 m^3 Density:1 kg/m^3 Weight:2.49455e-005 N | C:\Users\fenobus\OneDrive - City, University of London\SolidworksFiles\fs\18650\EndCap.SLDPRT Feb 26 18:34:28 2018
Boss-Extrude3 | Solid Body | Mass:1.70971e-005 kg Volume:1.70971e-005 m^3 Density:1 kg/m^3 Weight:0.000167551 N | C:\Users\fenobus\OneDrive - City, University of London\SolidworksFiles\fs\18650\HB2.SLDPRT Feb 25 17:30:42 2018
Boss-Extrude4 | Solid Body | Mass:2.54546e-006 kg Volume:2.54546e-006 m^3 Density:1 kg/m^3 Weight:2.49455e-005 N | C:\Users\fenobus\OneDrive - City, University of London\SolidworksFiles\fs\18650\EndCap.SLDPRT Feb 26 18:34:28 2018
Boss-Extrude4 | Solid Body | Mass:2.54546e-006 kg Volume:2.54546e-006 m^3 Density:1 kg/m^3 Weight:2.49455e-005 N | C:\Users\fenobus\OneDrive - City, University of London\SolidworksFiles\fs\18650\EndCap.SLDPRT Feb 26 18:34:28 2018
Boss-Extrude3 | Solid Body | Mass:1.70971e-005 kg Volume:1.70971e-005 m^3 Density:1 kg/m^3 Weight:0.000167551 N | C:\Users\fenobus\OneDrive - City, University of London\SolidworksFiles\fs\18650\HB2.SLDPRT Feb 25 17:30:42 2018
Boss-Extrude4 | Solid Body | Mass:2.54546e-006 kg Volume:2.54546e-006 m^3 Density:1 kg/m^3 Weight:2.49455e-005 N | C:\Users\fenobus\OneDrive - City, University of London\SolidworksFiles\fs\18650\EndCap.SLDPRT Feb 26 18:34:28 2018
Boss-Extrude4 | Solid Body | Mass:2.54546e-006 kg Volume:2.54546e-006 m^3 Density:1 kg/m^3 Weight:2.49455e-005 N | C:\Users\fenobus\OneDrive - City, University of London\SolidworksFiles\fs\18650\EndCap.SLDPRT Feb 26 18:34:28 2018
Boss-Extrude3 | Solid Body | Mass:1.70971e-005 kg Volume:1.70971e-005 m^3 Density:1 kg/m^3 Weight:0.000167551 N | C:\Users\fenobus\OneDrive - City, University of London\SolidworksFiles\fs\18650\HB2.SLDPRT Feb 25 17:30:42 2018
Boss-Extrude4 | Solid Body | Mass:2.54546e-006 kg Volume:2.54546e-006 m^3 Density:1 kg/m^3 Weight:2.49455e-005 N | C:\Users\fenobus\OneDrive - City, University of London\SolidworksFiles\fs\18650\EndCap.SLDPRT Feb 26 18:34:28 2018
Boss-Extrude4 | Solid Body | Mass:2.54546e-006 kg Volume:2.54546e-006 m^3 Density:1 kg/m^3 Weight:2.49455e-005 N | C:\Users\fenobus\OneDrive - City, University of London\SolidworksFiles\fs\18650\EndCap.SLDPRT Feb 26 18:34:28 2018
Boss-Extrude3 | Solid Body | Mass:1.70971e-005 kg Volume:1.70971e-005 m^3 Density:1 kg/m^3 Weight:0.000167551 N | C:\Users\fenobus\OneDrive - City, University of London\SolidworksFiles\fs\18650\HB2.SLDPRT Feb 25 17:30:42 2018
Boss-Extrude4 | Solid Body | Mass:2.54546e-006 kg Volume:2.54546e-006 m^3 Density:1 kg/m^3 Weight:2.49455e-005 N | C:\Users\fenobus\OneDrive - City, University of London\SolidworksFiles\fs\18650\EndCap.SLDPRT Feb 26 18:34:28 2018
Boss-Extrude4 | Solid Body | Mass:2.54546e-006 kg Volume:2.54546e-006 m^3 Density:1 kg/m^3 Weight:2.49455e-005 N | C:\Users\fenobus\OneDrive - City, University of London\SolidworksFiles\fs\18650\EndCap.SLDPRT Feb 26 18:34:28 2018
Boss-Extrude3 | Solid Body | Mass:1.70971e-005 kg Volume:1.70971e-005 m^3 Density:1 kg/m^3 Weight:0.000167551 N | C:\Users\fenobus\OneDrive - City, University of London\SolidworksFiles\fs\18650\HB2.SLDPRT Feb 25 17:30:42 2018
Boss-Extrude4 | Solid Body | Mass:2.54546e-006 kg Volume:2.54546e-006 m^3 Density:1 kg/m^3 Weight:2.49455e-005 N | C:\Users\fenobus\OneDrive - City, University of London\SolidworksFiles\fs\18650\EndCap.SLDPRT Feb 26 18:34:28 2018
Boss-Extrude4 | Solid Body | Mass:2.54546e-006 kg Volume:2.54546e-006 m^3 Density:1 kg/m^3 Weight:2.49455e-005 N | C:\Users\fenobus\OneDrive - City, University of London\SolidworksFiles\fs\18650\EndCap.SLDPRT Feb 26 18:34:28 2018
Boss-Extrude3 | Solid Body | Mass:1.70971e-005 kg Volume:1.70971e-005 m^3 Density:1 kg/m^3 Weight:0.000167551 N | C:\Users\fenobus\OneDrive - City, University of London\SolidworksFiles\fs\18650\HB2.SLDPRT Feb 25 17:30:42 2018
Boss-Extrude4 | Solid Body | Mass:2.54546e-006 kg Volume:2.54546e-006 m^3 Density:1 kg/m^3 Weight:2.49455e-005 N | C:\Users\fenobus\OneDrive - City, University of London\SolidworksFiles\fs\18650\EndCap.SLDPRT Feb 26 18:34:28 2018
Boss-Extrude4 | Solid Body | Mass:2.54546e-006 kg Volume:2.54546e-006 m^3 Density:1 kg/m^3 Weight:2.49455e-005 N | C:\Users\fenobus\OneDrive - City, University of London\SolidworksFiles\fs\18650\EndCap.SLDPRT Feb 26 18:34:28 2018
Boss-Extrude3 | Solid Body | Mass:1.70971e-005 kg Volume:1.70971e-005 m^3 Density:1 kg/m^3 Weight:0.000167551 N | C:\Users\fenobus\OneDrive - City, University of London\SolidworksFiles\fs\18650\HB2.SLDPRT Feb 25 17:30:42 2018
Boss-Extrude4 | Solid Body | Mass:2.54546e-006 kg Volume:2.54546e-006 m^3 Density:1 kg/m^3 Weight:2.49455e-005 N | C:\Users\fenobus\OneDrive - City, University of London\SolidworksFiles\fs\18650\EndCap.SLDPRT Feb 26 18:34:28 2018
Boss-Extrude4 | Solid Body | Mass:2.54546e-006 kg Volume:2.54546e-006 m^3 Density:1 kg/m^3 Weight:2.49455e-005 N | C:\Users\fenobus\OneDrive - City, University of London\SolidworksFiles\fs\18650\EndCap.SLDPRT Feb 26 18:34:28 2018
Boss-Extrude3 | Solid Body | Mass:1.70971e-005 kg Volume:1.70971e-005 m^3 Density:1 kg/m^3 Weight:0.000167551 N | C:\Users\fenobus\OneDrive - City, University of London\SolidworksFiles\fs\18650\HB2.SLDPRT Feb 25 17:30:42 2018
Boss-Extrude4 | Solid Body | Mass:2.54546e-006 kg Volume:2.54546e-006 m^3 Density:1 kg/m^3 Weight:2.49455e-005 N | C:\Users\fenobus\OneDrive - City, University of London\SolidworksFiles\fs\18650\EndCap.SLDPRT Feb 26 18:34:28 2018
Boss-Extrude4 | Solid Body | Mass:2.54546e-006 kg Volume:2.54546e-006 m^3 Density:1 kg/m^3 Weight:2.49455e-005 N | C:\Users\fenobus\OneDrive - City, University of London\SolidworksFiles\fs\18650\EndCap.SLDPRT Feb 26 18:34:28 2018
Boss-Extrude3 | Solid Body | Mass:1.70971e-005 kg Volume:1.70971e-005 m^3 Density:1 kg/m^3 Weight:0.000167551 N | C:\Users\fenobus\OneDrive - City, University of London\SolidworksFiles\fs\18650\HB2.SLDPRT Feb 25 17:30:42 2018
Boss-Extrude4 | Solid Body | Mass:2.54546e-006 kg Volume:2.54546e-006 m^3 Density:1 kg/m^3 Weight:2.49455e-005 N | C:\Users\fenobus\OneDrive - City, University of London\SolidworksFiles\fs\18650\EndCap.SLDPRT Feb 26 18:34:28 2018
Boss-Extrude4 | Solid Body | Mass:2.54546e-006 kg Volume:2.54546e-006 m^3 Density:1 kg/m^3 Weight:2.49455e-005 N | C:\Users\fenobus\OneDrive - City, University of London\SolidworksFiles\fs\18650\EndCap.SLDPRT Feb 26 18:34:28 2018
Boss-Extrude3 | Solid Body | Mass:1.70971e-005 kg Volume:1.70971e-005 m^3 Density:1 kg/m^3 Weight:0.000167551 N | C:\Users\fenobus\OneDrive - City, University of London\SolidworksFiles\fs\18650\HB2.SLDPRT Feb 25 17:30:42 2018
Boss-Extrude4 | Solid Body | Mass:2.54546e-006 kg Volume:2.54546e-006 m^3 Density:1 kg/m^3 Weight:2.49455e-005 N | C:\Users\fenobus\OneDrive - City, University of London\SolidworksFiles\fs\18650\EndCap.SLDPRT Feb 26 18:34:28 2018
Boss-Extrude4 | Solid Body | Mass:2.54546e-006 kg Volume:2.54546e-006 m^3 Density:1 kg/m^3 Weight:2.49455e-005 N | C:\Users\fenobus\OneDrive - City, University of London\SolidworksFiles\fs\18650\EndCap.SLDPRT Feb 26 18:34:28 2018
Boss-Extrude3 | Solid Body | Mass:1.70971e-005 kg Volume:1.70971e-005 m^3 Density:1 kg/m^3 Weight:0.000167551 N | C:\Users\fenobus\OneDrive - City, University of London\SolidworksFiles\fs\18650\HB2.SLDPRT Feb 25 17:30:42 2018
Boss-Extrude4 | Solid Body | Mass:2.54546e-006 kg Volume:2.54546e-006 m^3 Density:1 kg/m^3 Weight:2.49455e-005 N | C:\Users\fenobus\OneDrive - City, University of London\SolidworksFiles\fs\18650\EndCap.SLDPRT Feb 26 18:34:28 2018
Boss-Extrude4 | Solid Body | Mass:2.54546e-006 kg Volume:2.54546e-006 m^3 Density:1 kg/m^3 Weight:2.49455e-005 N | C:\Users\fenobus\OneDrive - City, University of London\SolidworksFiles\fs\18650\EndCap.SLDPRT Feb 26 18:34:28 2018
Boss-Extrude3 | Solid Body | Mass:1.70971e-005 kg Volume:1.70971e-005 m^3 Density:1 kg/m^3 Weight:0.000167551 N | C:\Users\fenobus\OneDrive - City, University of London\SolidworksFiles\fs\18650\HB2.SLDPRT Feb 25 17:30:42 2018
Boss-Extrude4 | Solid Body | Mass:2.54546e-006 kg Volume:2.54546e-006 m^3 Density:1 kg/m^3 Weight:2.49455e-005 N | C:\Users\fenobus\OneDrive - City, University of London\SolidworksFiles\fs\18650\EndCap.SLDPRT Feb 26 18:34:28 2018
Boss-Extrude4 | Solid Body | Mass:2.54546e-006 kg Volume:2.54546e-006 m^3 Density:1 kg/m^3 Weight:2.49455e-005 N | C:\Users\fenobus\OneDrive - City, University of London\SolidworksFiles\fs\18650\EndCap.SLDPRT Feb 26 18:34:28 2018
Boss-Extrude3 | Solid Body | Mass:1.70971e-005 kg Volume:1.70971e-005 m^3 Density:1 kg/m^3 Weight:0.000167551 N | C:\Users\fenobus\OneDrive - City, University of London\SolidworksFiles\fs\18650\HB2.SLDPRT Feb 25 17:30:42 2018
Boss-Extrude4 | Solid Body | Mass:2.54546e-006 kg Volume:2.54546e-006 m^3 Density:1 kg/m^3 Weight:2.49455e-005 N | C:\Users\fenobus\OneDrive - City, University of London\SolidworksFiles\fs\18650\EndCap.SLDPRT Feb 26 18:34:28 2018
Boss-Extrude4 | Solid Body | Mass:2.54546e-006 kg Volume:2.54546e-006 m^3 Density:1 kg/m^3 Weight:2.49455e-005 N | C:\Users\fenobus\OneDrive - City, University of London\SolidworksFiles\fs\18650\EndCap.SLDPRT Feb 26 18:34:28 2018
Boss-Extrude3 | Solid Body | Mass:1.70971e-005 kg Volume:1.70971e-005 m^3 Density:1 kg/m^3 Weight:0.000167551 N | C:\Users\fenobus\OneDrive - City, University of London\SolidworksFiles\fs\18650\HB2.SLDPRT Feb 25 17:30:42 2018
Boss-Extrude4 | Solid Body | Mass:2.54546e-006 kg Volume:2.54546e-006 m^3 Density:1 kg/m^3 Weight:2.49455e-005 N | C:\Users\fenobus\OneDrive - City, University of London\SolidworksFiles\fs\18650\EndCap.SLDPRT Feb 26 18:34:28 2018
Boss-Extrude4 | Solid Body | Mass:2.54546e-006 kg Volume:2.54546e-006 m^3 Density:1 kg/m^3 Weight:2.49455e-005 N | C:\Users\fenobus\OneDrive - City, University of London\SolidworksFiles\fs\18650\EndCap.SLDPRT Feb 26 18:34:28 2018
Boss-Extrude3 | Solid Body | Mass:1.70971e-005 kg Volume:1.70971e-005 m^3 Density:1 kg/m^3 Weight:0.000167551 N | C:\Users\fenobus\OneDrive - City, University of London\SolidworksFiles\fs\18650\HB2.SLDPRT Feb 25 17:30:42 2018
Boss-Extrude4 | Solid Body | Mass:2.54546e-006 kg Volume:2.54546e-006 m^3 Density:1 kg/m^3 Weight:2.49455e-005 N | C:\Users\fenobus\OneDrive - City, University of London\SolidworksFiles\fs\18650\EndCap.SLDPRT Feb 26 18:34:28 2018
Boss-Extrude4 | Solid Body | Mass:2.54546e-006 kg Volume:2.54546e-006 m^3 Density:1 kg/m^3 Weight:2.49455e-005 N | C:\Users\fenobus\OneDrive - City, University of London\SolidworksFiles\fs\18650\EndCap.SLDPRT Feb 26 18:34:28 2018
Boss-Extrude3 | Solid Body | Mass:1.70971e-005 kg Volume:1.70971e-005 m^3 Density:1 kg/m^3 Weight:0.000167551 N | C:\Users\fenobus\OneDrive - City, University of London\SolidworksFiles\fs\18650\HB2.SLDPRT Feb 25 17:30:42 2018
Boss-Extrude4 | Solid Body | Mass:2.54546e-006 kg Volume:2.54546e-006 m^3 Density:1 kg/m^3 Weight:2.49455e-005 N | C:\Users\fenobus\OneDrive - City, University of London\SolidworksFiles\fs\18650\EndCap.SLDPRT Feb 26 18:34:28 2018
Boss-Extrude4 | Solid Body | Mass:2.54546e-006 kg Volume:2.54546e-006 m^3 Density:1 kg/m^3 Weight:2.49455e-005 N | C:\Users\fenobus\OneDrive - City, University of London\SolidworksFiles\fs\18650\EndCap.SLDPRT Feb 26 18:34:28 2018
Boss-Extrude3 | Solid Body | Mass:1.70971e-005 kg Volume:1.70971e-005 m^3 Density:1 kg/m^3 Weight:0.000167551 N | C:\Users\fenobus\OneDrive - City, University of London\SolidworksFiles\fs\18650\HB2.SLDPRT Feb 25 17:30:42 2018
Boss-Extrude4 | Solid Body | Mass:2.54546e-006 kg Volume:2.54546e-006 m^3 Density:1 kg/m^3 Weight:2.49455e-005 N | C:\Users\fenobus\OneDrive - City, University of London\SolidworksFiles\fs\18650\EndCap.SLDPRT Feb 26 18:34:28 2018
Boss-Extrude4 | Solid Body | Mass:2.54546e-006 kg Volume:2.54546e-006 m^3 Density:1 kg/m^3 Weight:2.49455e-005 N | C:\Users\fenobus\OneDrive - City, University of London\SolidworksFiles\fs\18650\EndCap.SLDPRT Feb 26 18:34:28 2018
Boss-Extrude3 | Solid Body | Mass:1.70971e-005 kg Volume:1.70971e-005 m^3 Density:1 kg/m^3 Weight:0.000167551 N | C:\Users\fenobus\OneDrive - City, University of London\SolidworksFiles\fs\18650\HB2.SLDPRT Feb 25 17:30:42 2018
Boss-Extrude4 | Solid Body | Mass:2.54546e-006 kg Volume:2.54546e-006 m^3 Density:1 kg/m^3 Weight:2.49455e-005 N | C:\Users\fenobus\OneDrive - City, University of London\SolidworksFiles\fs\18650\EndCap.SLDPRT Feb 26 18:34:28 2018
Boss-Extrude4 | Solid Body | Mass:2.54546e-006 kg Volume:2.54546e-006 m^3 Density:1 kg/m^3 Weight:2.49455e-005 N | C:\Users\fenobus\OneDrive - City, University of London\SolidworksFiles\fs\18650\EndCap.SLDPRT Feb 26 18:34:28 2018
Boss-Extrude3 | Solid Body | Mass:1.70971e-005 kg Volume:1.70971e-005 m^3 Density:1 kg/m^3 Weight:0.000167551 N | C:\Users\fenobus\OneDrive - City, University of London\SolidworksFiles\fs\18650\HB2.SLDPRT Feb 25 17:30:42 2018
Boss-Extrude4 | Solid Body | Mass:2.54546e-006 kg Volume:2.54546e-006 m^3 Density:1 kg/m^3 Weight:2.49455e-005 N | C:\Users\fenobus\OneDrive - City, University of London\SolidworksFiles\fs\18650\EndCap.SLDPRT Feb 26 18:34:28 2018
Boss-Extrude4 | Solid Body | Mass:2.54546e-006 kg Volume:2.54546e-006 m^3 Density:1 kg/m^3 Weight:2.49455e-005 N | C:\Users\fenobus\OneDrive - City, University of London\SolidworksFiles\fs\18650\EndCap.SLDPRT Feb 26 18:34:28 2018
Boss-Extrude3 | Solid Body | Mass:1.70971e-005 kg Volume:1.70971e-005 m^3 Density:1 kg/m^3 Weight:0.000167551 N | C:\Users\fenobus\OneDrive - City, University of London\SolidworksFiles\fs\18650\HB2.SLDPRT Feb 25 17:30:42 2018
Boss-Extrude4 | Solid Body | Mass:2.54546e-006 kg Volume:2.54546e-006 m^3 Density:1 kg/m^3 Weight:2.49455e-005 N | C:\Users\fenobus\OneDrive - City, University of London\SolidworksFiles\fs\18650\EndCap.SLDPRT Feb 26 18:34:28 2018
Boss-Extrude4 | Solid Body | Mass:2.54546e-006 kg Volume:2.54546e-006 m^3 Density:1 kg/m^3 Weight:2.49455e-005 N | C:\Users\fenobus\OneDrive - City, University of London\SolidworksFiles\fs\18650\EndCap.SLDPRT Feb 26 18:34:28 2018
Boss-Extrude3 | Solid Body | Mass:1.70971e-005 kg Volume:1.70971e-005 m^3 Density:1 kg/m^3 Weight:0.000167551 N | C:\Users\fenobus\OneDrive - City, University of London\SolidworksFiles\fs\18650\HB2.SLDPRT Feb 25 17:30:42 2018
Boss-Extrude4 | Solid Body | Mass:2.54546e-006 kg Volume:2.54546e-006 m^3 Density:1 kg/m^3 Weight:2.49455e-005 N | C:\Users\fenobus\OneDrive - City, University of London\SolidworksFiles\fs\18650\EndCap.SLDPRT Feb 26 18:34:28 2018
Boss-Extrude4 | Solid Body | Mass:2.54546e-006 kg Volume:2.54546e-006 m^3 Density:1 kg/m^3 Weight:2.49455e-005 N | C:\Users\fenobus\OneDrive - City, University of London\SolidworksFiles\fs\18650\EndCap.SLDPRT Feb 26 18:34:28 2018
Boss-Extrude3 | Solid Body | Mass:1.70971e-005 kg Volume:1.70971e-005 m^3 Density:1 kg/m^3 Weight:0.000167551 N | C:\Users\fenobus\OneDrive - City, University of London\SolidworksFiles\fs\18650\HB2.SLDPRT Feb 25 17:30:42 2018
Boss-Extrude4 | Solid Body | Mass:2.54546e-006 kg Volume:2.54546e-006 m^3 Density:1 kg/m^3 Weight:2.49455e-005 N | C:\Users\fenobus\OneDrive - City, University of London\SolidworksFiles\fs\18650\EndCap.SLDPRT Feb 26 18:34:28 2018
Boss-Extrude4 | Solid Body | Mass:2.54546e-006 kg Volume:2.54546e-006 m^3 Density:1 kg/m^3 Weight:2.49455e-005 N | C:\Users\fenobus\OneDrive - City, University of London\SolidworksFiles\fs\18650\EndCap.SLDPRT Feb 26 18:34:28 2018
Boss-Extrude3 | Solid Body | Mass:1.70971e-005 kg Volume:1.70971e-005 m^3 Density:1 kg/m^3 Weight:0.000167551 N | C:\Users\fenobus\OneDrive - City, University of London\SolidworksFiles\fs\18650\HB2.SLDPRT Feb 25 17:30:42 2018
Boss-Extrude4 | Solid Body | Mass:2.54546e-006 kg Volume:2.54546e-006 m^3 Density:1 kg/m^3 Weight:2.49455e-005 N | C:\Users\fenobus\OneDrive - City, University of London\SolidworksFiles\fs\18650\EndCap.SLDPRT Feb 26 18:34:28 2018
Boss-Extrude4 | Solid Body | Mass:2.54546e-006 kg Volume:2.54546e-006 m^3 Density:1 kg/m^3 Weight:2.49455e-005 N | C:\Users\fenobus\OneDrive - City, University of London\SolidworksFiles\fs\18650\EndCap.SLDPRT Feb 26 18:34:28 2018
Boss-Extrude3 | Solid Body | Mass:1.70971e-005 kg Volume:1.70971e-005 m^3 Density:1 kg/m^3 Weight:0.000167551 N | C:\Users\fenobus\OneDrive - City, University of London\SolidworksFiles\fs\18650\HB2.SLDPRT Feb 25 17:30:42 2018
Boss-Extrude4 | Solid Body | Mass:2.54546e-006 kg Volume:2.54546e-006 m^3 Density:1 kg/m^3 Weight:2.49455e-005 N | C:\Users\fenobus\OneDrive - City, University of London\SolidworksFiles\fs\18650\EndCap.SLDPRT Feb 26 18:34:28 2018
Boss-Extrude4 | Solid Body | Mass:2.54546e-006 kg Volume:2.54546e-006 m^3 Density:1 kg/m^3 Weight:2.49455e-005 N | C:\Users\fenobus\OneDrive - City, University of London\SolidworksFiles\fs\18650\EndCap.SLDPRT Feb 26 18:34:28 2018
Boss-Extrude3 | Solid Body | Mass:1.70971e-005 kg Volume:1.70971e-005 m^3 Density:1 kg/m^3 Weight:0.000167551 N | C:\Users\fenobus\OneDrive - City, University of London\SolidworksFiles\fs\18650\HB2.SLDPRT Feb 25 17:30:42 2018
Boss-Extrude4 | Solid Body | Mass:2.54546e-006 kg Volume:2.54546e-006 m^3 Density:1 kg/m^3 Weight:2.49455e-005 N | C:\Users\fenobus\OneDrive - City, University of London\SolidworksFiles\fs\18650\EndCap.SLDPRT Feb 26 18:34:28 2018
Boss-Extrude4 | Solid Body | Mass:2.54546e-006 kg Volume:2.54546e-006 m^3 Density:1 kg/m^3 Weight:2.49455e-005 N | C:\Users\fenobus\OneDrive - City, University of London\SolidworksFiles\fs\18650\EndCap.SLDPRT Feb 26 18:34:28 2018
Boss-Extrude3 | Solid Body | Mass:1.70971e-005 kg Volume:1.70971e-005 m^3 Density:1 kg/m^3 Weight:0.000167551 N | C:\Users\fenobus\OneDrive - City, University of London\SolidworksFiles\fs\18650\HB2.SLDPRT Feb 25 17:30:42 2018
Boss-Extrude4 | Solid Body | Mass:2.54546e-006 kg Volume:2.54546e-006 m^3 Density:1 kg/m^3 Weight:2.49455e-005 N | C:\Users\fenobus\OneDrive - City, University of London\SolidworksFiles\fs\18650\EndCap.SLDPRT Feb 26 18:34:28 2018
Boss-Extrude4 | Solid Body | Mass:2.54546e-006 kg Volume:2.54546e-006 m^3 Density:1 kg/m^3 Weight:2.49455e-005 N | C:\Users\fenobus\OneDrive - City, University of London\SolidworksFiles\fs\18650\EndCap.SLDPRT Feb 26 18:34:28 2018
Boss-Extrude3 | Solid Body | Mass:1.70971e-005 kg Volume:1.70971e-005 m^3 Density:1 kg/m^3 Weight:0.000167551 N | C:\Users\fenobus\OneDrive - City, University of London\SolidworksFiles\fs\18650\HB2.SLDPRT Feb 25 17:30:42 2018
Boss-Extrude4 | Solid Body | Mass:2.54546e-006 kg Volume:2.54546e-006 m^3 Density:1 kg/m^3 Weight:2.49455e-005 N | C:\Users\fenobus\OneDrive - City, University of London\SolidworksFiles\fs\18650\EndCap.SLDPRT Feb 26 18:34:28 2018
Boss-Extrude4 | Solid Body | Mass:2.54546e-006 kg Volume:2.54546e-006 m^3 Density:1 kg/m^3 Weight:2.49455e-005 N | C:\Users\fenobus\OneDrive - City, University of London\SolidworksFiles\fs\18650\EndCap.SLDPRT Feb 26 18:34:28 2018
Boss-Extrude3 | Solid Body | Mass:1.70971e-005 kg Volume:1.70971e-005 m^3 Density:1 kg/m^3 Weight:0.000167551 N | C:\Users\fenobus\OneDrive - City, University of London\SolidworksFiles\fs\18650\HB2.SLDPRT Feb 25 17:30:42 2018
Boss-Extrude4 | Solid Body | Mass:2.54546e-006 kg Volume:2.54546e-006 m^3 Density:1 kg/m^3 Weight:2.49455e-005 N | C:\Users\fenobus\OneDrive - City, University of London\SolidworksFiles\fs\18650\EndCap.SLDPRT Feb 26 18:34:28 2018
Boss-Extrude4 | Solid Body | Mass:2.54546e-006 kg Volume:2.54546e-006 m^3 Density:1 kg/m^3 Weight:2.49455e-005 N | C:\Users\fenobus\OneDrive - City, University of London\SolidworksFiles\fs\18650\EndCap.SLDPRT Feb 26 18:34:28 2018
Boss-Extrude3 | Solid Body | Mass:1.70971e-005 kg Volume:1.70971e-005 m^3 Density:1 kg/m^3 Weight:0.000167551 N | C:\Users\fenobus\OneDrive - City, University of London\SolidworksFiles\fs\18650\HB2.SLDPRT Feb 25 17:30:42 2018
Boss-Extrude4 | Solid Body | Mass:2.54546e-006 kg Volume:2.54546e-006 m^3 Density:1 kg/m^3 Weight:2.49455e-005 N | C:\Users\fenobus\OneDrive - City, University of London\SolidworksFiles\fs\18650\EndCap.SLDPRT Feb 26 18:34:28 2018
Boss-Extrude4 | Solid Body | Mass:2.54546e-006 kg Volume:2.54546e-006 m^3 Density:1 kg/m^3 Weight:2.49455e-005 N | C:\Users\fenobus\OneDrive - City, University of London\SolidworksFiles\fs\18650\EndCap.SLDPRT Feb 26 18:34:28 2018
Boss-Extrude3 | Solid Body | Mass:1.70971e-005 kg Volume:1.70971e-005 m^3 Density:1 kg/m^3 Weight:0.000167551 N | C:\Users\fenobus\OneDrive - City, University of London\SolidworksFiles\fs\18650\HB2.SLDPRT Feb 25 17:30:42 2018
Boss-Extrude4 | Solid Body | Mass:2.54546e-006 kg Volume:2.54546e-006 m^3 Density:1 kg/m^3 Weight:2.49455e-005 N | C:\Users\fenobus\OneDrive - City, University of London\SolidworksFiles\fs\18650\EndCap.SLDPRT Feb 26 18:34:28 2018
Boss-Extrude4 | Solid Body | Mass:2.54546e-006 kg Volume:2.54546e-006 m^3 Density:1 kg/m^3 Weight:2.49455e-005 N | C:\Users\fenobus\OneDrive - City, University of London\SolidworksFiles\fs\18650\EndCap.SLDPRT Feb 26 18:34:28 2018
Boss-Extrude3 | Solid Body | Mass:1.70971e-005 kg Volume:1.70971e-005 m^3 Density:1 kg/m^3 Weight:0.000167551 N | C:\Users\fenobus\OneDrive - City, University of London\SolidworksFiles\fs\18650\HB2.SLDPRT Feb 25 17:30:42 2018
Boss-Extrude4 | Solid Body | Mass:2.54546e-006 kg Volume:2.54546e-006 m^3 Density:1 kg/m^3 Weight:2.49455e-005 N | C:\Users\fenobus\OneDrive - City, University of London\SolidworksFiles\fs\18650\EndCap.SLDPRT Feb 26 18:34:28 2018
Boss-Extrude4 | Solid Body | Mass:2.54546e-006 kg Volume:2.54546e-006 m^3 Density:1 kg/m^3 Weight:2.49455e-005 N | C:\Users\fenobus\OneDrive - City, University of London\SolidworksFiles\fs\18650\EndCap.SLDPRT Feb 26 18:34:28 2018
Boss-Extrude3 | Solid Body | Mass:1.70971e-005 kg Volume:1.70971e-005 m^3 Density:1 kg/m^3 Weight:0.000167551 N | C:\Users\fenobus\OneDrive - City, University of London\SolidworksFiles\fs\18650\HB2.SLDPRT Feb 25 17:30:42 2018
Boss-Extrude4 | Solid Body | Mass:2.54546e-006 kg Volume:2.54546e-006 m^3 Density:1 kg/m^3 Weight:2.49455e-005 N | C:\Users\fenobus\OneDrive - City, University of London\SolidworksFiles\fs\18650\EndCap.SLDPRT Feb 26 18:34:28 2018
Boss-Extrude4 | Solid Body | Mass:2.54546e-006 kg Volume:2.54546e-006 m^3 Density:1 kg/m^3 Weight:2.49455e-005 N | C:\Users\fenobus\OneDrive - City, University of London\SolidworksFiles\fs\18650\EndCap.SLDPRT Feb 26 18:34:28 2018
Boss-Extrude3 | Solid Body | Mass:1.70971e-005 kg Volume:1.70971e-005 m^3 Density:1 kg/m^3 Weight:0.000167551 N | C:\Users\fenobus\OneDrive - City, University of London\SolidworksFiles\fs\18650\HB2.SLDPRT Feb 25 17:30:42 2018
Boss-Extrude4 | Solid Body | Mass:2.54546e-006 kg Volume:2.54546e-006 m^3 Density:1 kg/m^3 Weight:2.49455e-005 N | C:\Users\fenobus\OneDrive - City, University of London\SolidworksFiles\fs\18650\EndCap.SLDPRT Feb 26 18:34:28 2018
Boss-Extrude4 | Solid Body | Mass:2.54546e-006 kg Volume:2.54546e-006 m^3 Density:1 kg/m^3 Weight:2.49455e-005 N | C:\Users\fenobus\OneDrive - City, University of London\SolidworksFiles\fs\18650\EndCap.SLDPRT Feb 26 18:34:28 2018
Boss-Extrude3 | Solid Body | Mass:1.70971e-005 kg Volume:1.70971e-005 m^3 Density:1 kg/m^3 Weight:0.000167551 N | C:\Users\fenobus\OneDrive - City, University of London\SolidworksFiles\fs\18650\HB2.SLDPRT Feb 25 17:30:42 2018
Boss-Extrude4 | Solid Body | Mass:2.54546e-006 kg Volume:2.54546e-006 m^3 Density:1 kg/m^3 Weight:2.49455e-005 N | C:\Users\fenobus\OneDrive - City, University of London\SolidworksFiles\fs\18650\EndCap.SLDPRT Feb 26 18:34:28 2018
Boss-Extrude4 | Solid Body | Mass:2.54546e-006 kg Volume:2.54546e-006 m^3 Density:1 kg/m^3 Weight:2.49455e-005 N | C:\Users\fenobus\OneDrive - City, University of London\SolidworksFiles\fs\18650\EndCap.SLDPRT Feb 26 18:34:28 2018
Boss-Extrude3 | Solid Body | Mass:1.70971e-005 kg Volume:1.70971e-005 m^3 Density:1 kg/m^3 Weight:0.000167551 N | C:\Users\fenobus\OneDrive - City, University of London\SolidworksFiles\fs\18650\HB2.SLDPRT Feb 25 17:30:42 2018
Boss-Extrude4 | Solid Body | Mass:2.54546e-006 kg Volume:2.54546e-006 m^3 Density:1 kg/m^3 Weight:2.49455e-005 N | C:\Users\fenobus\OneDrive - City, University of London\SolidworksFiles\fs\18650\EndCap.SLDPRT Feb 26 18:34:28 2018
Boss-Extrude4 | Solid Body | Mass:2.54546e-006 kg Volume:2.54546e-006 m^3 Density:1 kg/m^3 Weight:2.49455e-005 N | C:\Users\fenobus\OneDrive - City, University of London\SolidworksFiles\fs\18650\EndCap.SLDPRT Feb 26 18:34:28 2018
Boss-Extrude3 | Solid Body | Mass:1.70971e-005 kg Volume:1.70971e-005 m^3 Density:1 kg/m^3 Weight:0.000167551 N | C:\Users\fenobus\OneDrive - City, University of London\SolidworksFiles\fs\18650\HB2.SLDPRT Feb 25 17:30:42 2018
Boss-Extrude4 | Solid Body | Mass:2.54546e-006 kg Volume:2.54546e-006 m^3 Density:1 kg/m^3 Weight:2.49455e-005 N | C:\Users\fenobus\OneDrive - City, University of London\SolidworksFiles\fs\18650\EndCap.SLDPRT Feb 26 18:34:28 2018
Boss-Extrude4 | Solid Body | Mass:2.54546e-006 kg Volume:2.54546e-006 m^3 Density:1 kg/m^3 Weight:2.49455e-005 N | C:\Users\fenobus\OneDrive - City, University of London\SolidworksFiles\fs\18650\EndCap.SLDPRT Feb 26 18:34:28 2018
Boss-Extrude3 | Solid Body | Mass:1.70971e-005 kg Volume:1.70971e-005 m^3 Density:1 kg/m^3 Weight:0.000167551 N | C:\Users\fenobus\OneDrive - City, University of London\SolidworksFiles\fs\18650\HB2.SLDPRT Feb 25 17:30:42 2018
Boss-Extrude4 | Solid Body | Mass:2.54546e-006 kg Volume:2.54546e-006 m^3 Density:1 kg/m^3 Weight:2.49455e-005 N | C:\Users\fenobus\OneDrive - City, University of London\SolidworksFiles\fs\18650\EndCap.SLDPRT Feb 26 18:34:28 2018
Boss-Extrude4 | Solid Body | Mass:2.54546e-006 kg Volume:2.54546e-006 m^3 Density:1 kg/m^3 Weight:2.49455e-005 N | C:\Users\fenobus\OneDrive - City, University of London\SolidworksFiles\fs\18650\EndCap.SLDPRT Feb 26 18:34:28 2018
Boss-Extrude3 | Solid Body | Mass:1.70971e-005 kg Volume:1.70971e-005 m^3 Density:1 kg/m^3 Weight:0.000167551 N | C:\Users\fenobus\OneDrive - City, University of London\SolidworksFiles\fs\18650\HB2.SLDPRT Feb 25 17:30:42 2018
Boss-Extrude4 | Solid Body | Mass:2.54546e-006 kg Volume:2.54546e-006 m^3 Density:1 kg/m^3 Weight:2.49455e-005 N | C:\Users\fenobus\OneDrive - City, University of London\SolidworksFiles\fs\18650\EndCap.SLDPRT Feb 26 18:34:28 2018
Boss-Extrude4 | Solid Body | Mass:2.54546e-006 kg Volume:2.54546e-006 m^3 Density:1 kg/m^3 Weight:2.49455e-005 N | C:\Users\fenobus\OneDrive - City, University of London\SolidworksFiles\fs\18650\EndCap.SLDPRT Feb 26 18:34:28 2018
Boss-Extrude3 | Solid Body | Mass:1.70971e-005 kg Volume:1.70971e-005 m^3 Density:1 kg/m^3 Weight:0.000167551 N | C:\Users\fenobus\OneDrive - City, University of London\SolidworksFiles\fs\18650\HB2.SLDPRT Feb 25 17:30:42 2018
Boss-Extrude4 | Solid Body | Mass:2.54546e-006 kg Volume:2.54546e-006 m^3 Density:1 kg/m^3 Weight:2.49455e-005 N | C:\Users\fenobus\OneDrive - City, University of London\SolidworksFiles\fs\18650\EndCap.SLDPRT Feb 26 18:34:28 2018
Boss-Extrude4 | Solid Body | Mass:2.54546e-006 kg Volume:2.54546e-006 m^3 Density:1 kg/m^3 Weight:2.49455e-005 N | C:\Users\fenobus\OneDrive - City, University of London\SolidworksFiles\fs\18650\EndCap.SLDPRT Feb 26 18:34:28 2018
Boss-Extrude3 | Solid Body | Mass:1.70971e-005 kg Volume:1.70971e-005 m^3 Density:1 kg/m^3 Weight:0.000167551 N | C:\Users\fenobus\OneDrive - City, University of London\SolidworksFiles\fs\18650\HB2.SLDPRT Feb 25 17:30:42 2018
Boss-Extrude4 | Solid Body | Mass:2.54546e-006 kg Volume:2.54546e-006 m^3 Density:1 kg/m^3 Weight:2.49455e-005 N | C:\Users\fenobus\OneDrive - City, University of London\SolidworksFiles\fs\18650\EndCap.SLDPRT Feb 26 18:34:28 2018
Boss-Extrude4 | Solid Body | Mass:2.54546e-006 kg Volume:2.54546e-006 m^3 Density:1 kg/m^3 Weight:2.49455e-005 N | C:\Users\fenobus\OneDrive - City, University of London\SolidworksFiles\fs\18650\EndCap.SLDPRT Feb 26 18:34:28 2018
Boss-Extrude3 | Solid Body | Mass:1.70971e-005 kg Volume:1.70971e-005 m^3 Density:1 kg/m^3 Weight:0.000167551 N | C:\Users\fenobus\OneDrive - City, University of London\SolidworksFiles\fs\18650\HB2.SLDPRT Feb 25 17:30:42 2018
Boss-Extrude4 | Solid Body | Mass:2.54546e-006 kg Volume:2.54546e-006 m^3 Density:1 kg/m^3 Weight:2.49455e-005 N | C:\Users\fenobus\OneDrive - City, University of London\SolidworksFiles\fs\18650\EndCap.SLDPRT Feb 26 18:34:28 2018
Boss-Extrude4 | Solid Body | Mass:2.54546e-006 kg Volume:2.54546e-006 m^3 Density:1 kg/m^3 Weight:2.49455e-005 N | C:\Users\fenobus\OneDrive - City, University of London\SolidworksFiles\fs\18650\EndCap.SLDPRT Feb 26 18:34:28 2018
Boss-Extrude3 | Solid Body | Mass:1.70971e-005 kg Volume:1.70971e-005 m^3 Density:1 kg/m^3 Weight:0.000167551 N | C:\Users\fenobus\OneDrive - City, University of London\SolidworksFiles\fs\18650\HB2.SLDPRT Feb 25 17:30:42 2018
Boss-Extrude4 | Solid Body | Mass:2.54546e-006 kg Volume:2.54546e-006 m^3 Density:1 kg/m^3 Weight:2.49455e-005 N | C:\Users\fenobus\OneDrive - City, University of London\SolidworksFiles\fs\18650\EndCap.SLDPRT Feb 26 18:34:28 2018
Boss-Extrude4 | Solid Body | Mass:2.54546e-006 kg Volume:2.54546e-006 m^3 Density:1 kg/m^3 Weight:2.49455e-005 N | C:\Users\fenobus\OneDrive - City, University of London\SolidworksFiles\fs\18650\EndCap.SLDPRT Feb 26 18:34:28 2018
Boss-Extrude3 | Solid Body | Mass:1.70971e-005 kg Volume:1.70971e-005 m^3 Density:1 kg/m^3 Weight:0.000167551 N | C:\Users\fenobus\OneDrive - City, University of London\SolidworksFiles\fs\18650\HB2.SLDPRT Feb 25 17:30:42 2018
Boss-Extrude4 | Solid Body | Mass:2.54546e-006 kg Volume:2.54546e-006 m^3 Density:1 kg/m^3 Weight:2.49455e-005 N | C:\Users\fenobus\OneDrive - City, University of London\SolidworksFiles\fs\18650\EndCap.SLDPRT Feb 26 18:34:28 2018
Boss-Extrude4 | Solid Body | Mass:2.54546e-006 kg Volume:2.54546e-006 m^3 Density:1 kg/m^3 Weight:2.49455e-005 N | C:\Users\fenobus\OneDrive - City, University of London\SolidworksFiles\fs\18650\EndCap.SLDPRT Feb 26 18:34:28 2018
Boss-Extrude3 | Solid Body | Mass:1.70971e-005 kg Volume:1.70971e-005 m^3 Density:1 kg/m^3 Weight:0.000167551 N | C:\Users\fenobus\OneDrive - City, University of London\SolidworksFiles\fs\18650\HB2.SLDPRT Feb 25 17:30:42 2018
Boss-Extrude4 | Solid Body | Mass:2.54546e-006 kg Volume:2.54546e-006 m^3 Density:1 kg/m^3 Weight:2.49455e-005 N | C:\Users\fenobus\OneDrive - City, University of London\SolidworksFiles\fs\18650\EndCap.SLDPRT Feb 26 18:34:28 2018
Boss-Extrude4 | Solid Body | Mass:2.54546e-006 kg Volume:2.54546e-006 m^3 Density:1 kg/m^3 Weight:2.49455e-005 N | C:\Users\fenobus\OneDrive - City, University of London\SolidworksFiles\fs\18650\EndCap.SLDPRT Feb 26 18:34:28 2018
Boss-Extrude3 | Solid Body | Mass:1.70971e-005 kg Volume:1.70971e-005 m^3 Density:1 kg/m^3 Weight:0.000167551 N | C:\Users\fenobus\OneDrive - City, University of London\SolidworksFiles\fs\18650\HB2.SLDPRT Feb 25 17:30:42 2018
Boss-Extrude4 | Solid Body | Mass:2.54546e-006 kg Volume:2.54546e-006 m^3 Density:1 kg/m^3 Weight:2.49455e-005 N | C:\Users\fenobus\OneDrive - City, University of London\SolidworksFiles\fs\18650\EndCap.SLDPRT Feb 26 18:34:28 2018
Boss-Extrude4 | Solid Body | Mass:2.54546e-006 kg Volume:2.54546e-006 m^3 Density:1 kg/m^3 Weight:2.49455e-005 N | C:\Users\fenobus\OneDrive - City, University of London\SolidworksFiles\fs\18650\EndCap.SLDPRT Feb 26 18:34:28 2018
Boss-Extrude3 | Solid Body | Mass:1.70971e-005 kg Volume:1.70971e-005 m^3 Density:1 kg/m^3 Weight:0.000167551 N | C:\Users\fenobus\OneDrive - City, University of London\SolidworksFiles\fs\18650\HB2.SLDPRT Feb 25 17:30:42 2018
Boss-Extrude4 | Solid Body | Mass:2.54546e-006 kg Volume:2.54546e-006 m^3 Density:1 kg/m^3 Weight:2.49455e-005 N | C:\Users\fenobus\OneDrive - City, University of London\SolidworksFiles\fs\18650\EndCap.SLDPRT Feb 26 18:34:28 2018
Boss-Extrude4 | Solid Body | Mass:2.54546e-006 kg Volume:2.54546e-006 m^3 Density:1 kg/m^3 Weight:2.49455e-005 N | C:\Users\fenobus\OneDrive - City, University of London\SolidworksFiles\fs\18650\EndCap.SLDPRT Feb 26 18:34:28 2018
Boss-Extrude3 | Solid Body | Mass:1.70971e-005 kg Volume:1.70971e-005 m^3 Density:1 kg/m^3 Weight:0.000167551 N | C:\Users\fenobus\OneDrive - City, University of London\SolidworksFiles\fs\18650\HB2.SLDPRT Feb 25 17:30:42 2018
Boss-Extrude4 | Solid Body | Mass:2.54546e-006 kg Volume:2.54546e-006 m^3 Density:1 kg/m^3 Weight:2.49455e-005 N | C:\Users\fenobus\OneDrive - City, University of London\SolidworksFiles\fs\18650\EndCap.SLDPRT Feb 26 18:34:28 2018
Boss-Extrude4 | Solid Body | Mass:2.54546e-006 kg Volume:2.54546e-006 m^3 Density:1 kg/m^3 Weight:2.49455e-005 N | C:\Users\fenobus\OneDrive - City, University of London\SolidworksFiles\fs\18650\EndCap.SLDPRT Feb 26 18:34:28 2018
Boss-Extrude3 | Solid Body | Mass:1.70971e-005 kg Volume:1.70971e-005 m^3 Density:1 kg/m^3 Weight:0.000167551 N | C:\Users\fenobus\OneDrive - City, University of London\SolidworksFiles\fs\18650\HB2.SLDPRT Feb 25 17:30:42 2018
Boss-Extrude4 | Solid Body | Mass:2.54546e-006 kg Volume:2.54546e-006 m^3 Density:1 kg/m^3 Weight:2.49455e-005 N | C:\Users\fenobus\OneDrive - City, University of London\SolidworksFiles\fs\18650\EndCap.SLDPRT Feb 26 18:34:28 2018
Boss-Extrude4 | Solid Body | Mass:2.54546e-006 kg Volume:2.54546e-006 m^3 Density:1 kg/m^3 Weight:2.49455e-005 N | C:\Users\fenobus\OneDrive - City, University of London\SolidworksFiles\fs\18650\EndCap.SLDPRT Feb 26 18:34:28 2018
Boss-Extrude3 | Solid Body | Mass:1.70971e-005 kg Volume:1.70971e-005 m^3 Density:1 kg/m^3 Weight:0.000167551 N | C:\Users\fenobus\OneDrive - City, University of London\SolidworksFiles\fs\18650\HB2.SLDPRT Feb 25 17:30:42 2018
Boss-Extrude4 | Solid Body | Mass:2.54546e-006 kg Volume:2.54546e-006 m^3 Density:1 kg/m^3 Weight:2.49455e-005 N | C:\Users\fenobus\OneDrive - City, University of London\SolidworksFiles\fs\18650\EndCap.SLDPRT Feb 26 18:34:28 2018
Boss-Extrude4 | Solid Body | Mass:2.54546e-006 kg Volume:2.54546e-006 m^3 Density:1 kg/m^3 Weight:2.49455e-005 N | C:\Users\fenobus\OneDrive - City, University of London\SolidworksFiles\fs\18650\EndCap.SLDPRT Feb 26 18:34:28 2018
Boss-Extrude3 | Solid Body | Mass:1.70971e-005 kg Volume:1.70971e-005 m^3 Density:1 kg/m^3 Weight:0.000167551 N | C:\Users\fenobus\OneDrive - City, University of London\SolidworksFiles\fs\18650\HB2.SLDPRT Feb 25 17:30:42 2018
Boss-Extrude4 | Solid Body | Mass:2.54546e-006 kg Volume:2.54546e-006 m^3 Density:1 kg/m^3 Weight:2.49455e-005 N | C:\Users\fenobus\OneDrive - City, University of London\SolidworksFiles\fs\18650\EndCap.SLDPRT Feb 26 18:34:28 2018
Boss-Extrude4 | Solid Body | Mass:2.54546e-006 kg Volume:2.54546e-006 m^3 Density:1 kg/m^3 Weight:2.49455e-005 N | C:\Users\fenobus\OneDrive - City, University of London\SolidworksFiles\fs\18650\EndCap.SLDPRT Feb 26 18:34:28 2018
Boss-Extrude3 | Solid Body | Mass:1.70971e-005 kg Volume:1.70971e-005 m^3 Density:1 kg/m^3 Weight:0.000167551 N | C:\Users\fenobus\OneDrive - City, University of London\SolidworksFiles\fs\18650\HB2.SLDPRT Feb 25 17:30:42 2018
Boss-Extrude4 | Solid Body | Mass:2.54546e-006 kg Volume:2.54546e-006 m^3 Density:1 kg/m^3 Weight:2.49455e-005 N | C:\Users\fenobus\OneDrive - City, University of London\SolidworksFiles\fs\18650\EndCap.SLDPRT Feb 26 18:34:28 2018
Boss-Extrude4 | Solid Body | Mass:2.54546e-006 kg Volume:2.54546e-006 m^3 Density:1 kg/m^3 Weight:2.49455e-005 N | C:\Users\fenobus\OneDrive - City, University of London\SolidworksFiles\fs\18650\EndCap.SLDPRT Feb 26 18:34:28 2018
Boss-Extrude3 | Solid Body | Mass:1.70971e-005 kg Volume:1.70971e-005 m^3 Density:1 kg/m^3 Weight:0.000167551 N | C:\Users\fenobus\OneDrive - City, University of London\SolidworksFiles\fs\18650\HB2.SLDPRT Feb 25 17:30:42 2018
Boss-Extrude4 | Solid Body | Mass:2.54546e-006 kg Volume:2.54546e-006 m^3 Density:1 kg/m^3 Weight:2.49455e-005 N | C:\Users\fenobus\OneDrive - City, University of London\SolidworksFiles\fs\18650\EndCap.SLDPRT Feb 26 18:34:28 2018
Boss-Extrude4 | Solid Body | Mass:2.54546e-006 kg Volume:2.54546e-006 m^3 Density:1 kg/m^3 Weight:2.49455e-005 N | C:\Users\fenobus\OneDrive - City, University of London\SolidworksFiles\fs\18650\EndCap.SLDPRT Feb 26 18:34:28 2018
Boss-Extrude3 | Solid Body | Mass:1.70971e-005 kg Volume:1.70971e-005 m^3 Density:1 kg/m^3 Weight:0.000167551 N | C:\Users\fenobus\OneDrive - City, University of London\SolidworksFiles\fs\18650\HB2.SLDPRT Feb 25 17:30:42 2018
Boss-Extrude4 | Solid Body | Mass:2.54546e-006 kg Volume:2.54546e-006 m^3 Density:1 kg/m^3 Weight:2.49455e-005 N | C:\Users\fenobus\OneDrive - City, University of London\SolidworksFiles\fs\18650\EndCap.SLDPRT Feb 26 18:34:28 2018
Boss-Extrude4 | Solid Body | Mass:2.54546e-006 kg Volume:2.54546e-006 m^3 Density:1 kg/m^3 Weight:2.49455e-005 N | C:\Users\fenobus\OneDrive - City, University of London\SolidworksFiles\fs\18650\EndCap.SLDPRT Feb 26 18:34:28 2018
Boss-Extrude3 | Solid Body | Mass:1.70971e-005 kg Volume:1.70971e-005 m^3 Density:1 kg/m^3 Weight:0.000167551 N | C:\Users\fenobus\OneDrive - City, University of London\SolidworksFiles\fs\18650\HB2.SLDPRT Feb 25 17:30:42 2018
Boss-Extrude4 | Solid Body | Mass:2.54546e-006 kg Volume:2.54546e-006 m^3 Density:1 kg/m^3 Weight:2.49455e-005 N | C:\Users\fenobus\OneDrive - City, University of London\SolidworksFiles\fs\18650\EndCap.SLDPRT Feb 26 18:34:28 2018
Boss-Extrude4 | Solid Body | Mass:2.54546e-006 kg Volume:2.54546e-006 m^3 Density:1 kg/m^3 Weight:2.49455e-005 N | C:\Users\fenobus\OneDrive - City, University of London\SolidworksFiles\fs\18650\EndCap.SLDPRT Feb 26 18:34:28 2018
Boss-Extrude3 | Solid Body | Mass:1.70971e-005 kg Volume:1.70971e-005 m^3 Density:1 kg/m^3 Weight:0.000167551 N | C:\Users\fenobus\OneDrive - City, University of London\SolidworksFiles\fs\18650\HB2.SLDPRT Feb 25 17:30:42 2018
Boss-Extrude4 | Solid Body | Mass:2.54546e-006 kg Volume:2.54546e-006 m^3 Density:1 kg/m^3 Weight:2.49455e-005 N | C:\Users\fenobus\OneDrive - City, University of London\SolidworksFiles\fs\18650\EndCap.SLDPRT Feb 26 18:34:28 2018
Boss-Extrude4 | Solid Body | Mass:2.54546e-006 kg Volume:2.54546e-006 m^3 Density:1 kg/m^3 Weight:2.49455e-005 N | C:\Users\fenobus\OneDrive - City, University of London\SolidworksFiles\fs\18650\EndCap.SLDPRT Feb 26 18:34:28 2018
Boss-Extrude3 | Solid Body | Mass:1.70971e-005 kg Volume:1.70971e-005 m^3 Density:1 kg/m^3 Weight:0.000167551 N | C:\Users\fenobus\OneDrive - City, University of London\SolidworksFiles\fs\18650\HB2.SLDPRT Feb 25 17:30:42 2018
Boss-Extrude4 | Solid Body | Mass:2.54546e-006 kg Volume:2.54546e-006 m^3 Density:1 kg/m^3 Weight:2.49455e-005 N | C:\Users\fenobus\OneDrive - City, University of London\SolidworksFiles\fs\18650\EndCap.SLDPRT Feb 26 18:34:28 2018
Boss-Extrude4 | Solid Body | Mass:2.54546e-006 kg Volume:2.54546e-006 m^3 Density:1 kg/m^3 Weight:2.49455e-005 N | C:\Users\fenobus\OneDrive - City, University of London\SolidworksFiles\fs\18650\EndCap.SLDPRT Feb 26 18:34:28 2018
Boss-Extrude3 | Solid Body | Mass:1.70971e-005 kg Volume:1.70971e-005 m^3 Density:1 kg/m^3 Weight:0.000167551 N | C:\Users\fenobus\OneDrive - City, University of London\SolidworksFiles\fs\18650\HB2.SLDPRT Feb 25 17:30:42 2018
Boss-Extrude4 | Solid Body | Mass:2.54546e-006 kg Volume:2.54546e-006 m^3 Density:1 kg/m^3 Weight:2.49455e-005 N | C:\Users\fenobus\OneDrive - City, University of London\SolidworksFiles\fs\18650\EndCap.SLDPRT Feb 26 18:34:28 2018
Boss-Extrude4 | Solid Body | Mass:2.54546e-006 kg Volume:2.54546e-006 m^3 Density:1 kg/m^3 Weight:2.49455e-005 N | C:\Users\fenobus\OneDrive - City, University of London\SolidworksFiles\fs\18650\EndCap.SLDPRT Feb 26 18:34:28 2018
Boss-Extrude3 | Solid Body | Mass:1.70971e-005 kg Volume:1.70971e-005 m^3 Density:1 kg/m^3 Weight:0.000167551 N | C:\Users\fenobus\OneDrive - City, University of London\SolidworksFiles\fs\18650\HB2.SLDPRT Feb 25 17:30:42 2018
Boss-Extrude4 | Solid Body | Mass:2.54546e-006 kg Volume:2.54546e-006 m^3 Density:1 kg/m^3 Weight:2.49455e-005 N | C:\Users\fenobus\OneDrive - City, University of London\SolidworksFiles\fs\18650\EndCap.SLDPRT Feb 26 18:34:28 2018
Boss-Extrude4 | Solid Body | Mass:2.54546e-006 kg Volume:2.54546e-006 m^3 Density:1 kg/m^3 Weight:2.49455e-005 N | C:\Users\fenobus\OneDrive - City, University of London\SolidworksFiles\fs\18650\EndCap.SLDPRT Feb 26 18:34:28 2018
Boss-Extrude3 | Solid Body | Mass:1.70971e-005 kg Volume:1.70971e-005 m^3 Density:1 kg/m^3 Weight:0.000167551 N | C:\Users\fenobus\OneDrive - City, University of London\SolidworksFiles\fs\18650\HB2.SLDPRT Feb 25 17:30:42 2018
Boss-Extrude4 | Solid Body | Mass:2.54546e-006 kg Volume:2.54546e-006 m^3 Density:1 kg/m^3 Weight:2.49455e-005 N | C:\Users\fenobus\OneDrive - City, University of London\SolidworksFiles\fs\18650\EndCap.SLDPRT Feb 26 18:34:28 2018
Boss-Extrude4 | Solid Body | Mass:2.54546e-006 kg Volume:2.54546e-006 m^3 Density:1 kg/m^3 Weight:2.49455e-005 N | C:\Users\fenobus\OneDrive - City, University of London\SolidworksFiles\fs\18650\EndCap.SLDPRT Feb 26 18:34:28 2018
Boss-Extrude3 | Solid Body | Mass:1.70971e-005 kg Volume:1.70971e-005 m^3 Density:1 kg/m^3 Weight:0.000167551 N | C:\Users\fenobus\OneDrive - City, University of London\SolidworksFiles\fs\18650\HB2.SLDPRT Feb 25 17:30:42 2018
Boss-Extrude4 | Solid Body | Mass:2.54546e-006 kg Volume:2.54546e-006 m^3 Density:1 kg/m^3 Weight:2.49455e-005 N | C:\Users\fenobus\OneDrive - City, University of London\SolidworksFiles\fs\18650\EndCap.SLDPRT Feb 26 18:34:28 2018
Boss-Extrude4 | Solid Body | Mass:2.54546e-006 kg Volume:2.54546e-006 m^3 Density:1 kg/m^3 Weight:2.49455e-005 N | C:\Users\fenobus\OneDrive - City, University of London\SolidworksFiles\fs\18650\EndCap.SLDPRT Feb 26 18:34:28 2018
Boss-Extrude3 | Solid Body | Mass:1.70971e-005 kg Volume:1.70971e-005 m^3 Density:1 kg/m^3 Weight:0.000167551 N | C:\Users\fenobus\OneDrive - City, University of London\SolidworksFiles\fs\18650\HB2.SLDPRT Feb 25 17:30:42 2018
Boss-Extrude4 | Solid Body | Mass:2.54546e-006 kg Volume:2.54546e-006 m^3 Density:1 kg/m^3 Weight:2.49455e-005 N | C:\Users\fenobus\OneDrive - City, University of London\SolidworksFiles\fs\18650\EndCap.SLDPRT Feb 26 18:34:28 2018
Boss-Extrude4 | Solid Body | Mass:2.54546e-006 kg Volume:2.54546e-006 m^3 Density:1 kg/m^3 Weight:2.49455e-005 N | C:\Users\fenobus\OneDrive - City, University of London\SolidworksFiles\fs\18650\EndCap.SLDPRT Feb 26 18:34:28 2018
Boss-Extrude3 | Solid Body | Mass:1.70971e-005 kg Volume:1.70971e-005 m^3 Density:1 kg/m^3 Weight:0.000167551 N | C:\Users\fenobus\OneDrive - City, University of London\SolidworksFiles\fs\18650\HB2.SLDPRT Feb 25 17:30:42 2018
Boss-Extrude4 | Solid Body | Mass:2.54546e-006 kg Volume:2.54546e-006 m^3 Density:1 kg/m^3 Weight:2.49455e-005 N | C:\Users\fenobus\OneDrive - City, University of London\SolidworksFiles\fs\18650\EndCap.SLDPRT Feb 26 18:34:28 2018
Boss-Extrude4 | Solid Body | Mass:2.54546e-006 kg Volume:2.54546e-006 m^3 Density:1 kg/m^3 Weight:2.49455e-005 N | C:\Users\fenobus\OneDrive - City, University of London\SolidworksFiles\fs\18650\EndCap.SLDPRT Feb 26 18:34:28 2018
Boss-Extrude3 | Solid Body | Mass:1.70971e-005 kg Volume:1.70971e-005 m^3 Density:1 kg/m^3 Weight:0.000167551 N | C:\Users\fenobus\OneDrive - City, University of London\SolidworksFiles\fs\18650\HB2.SLDPRT Feb 25 17:30:42 2018
Boss-Extrude4 | Solid Body | Mass:2.54546e-006 kg Volume:2.54546e-006 m^3 Density:1 kg/m^3 Weight:2.49455e-005 N | C:\Users\fenobus\OneDrive - City, University of London\SolidworksFiles\fs\18650\EndCap.SLDPRT Feb 26 18:34:28 2018
Boss-Extrude4 | Solid Body | Mass:2.54546e-006 kg Volume:2.54546e-006 m^3 Density:1 kg/m^3 Weight:2.49455e-005 N | C:\Users\fenobus\OneDrive - City, University of London\SolidworksFiles\fs\18650\EndCap.SLDPRT Feb 26 18:34:28 2018
Boss-Extrude3 | Solid Body | Mass:1.70971e-005 kg Volume:1.70971e-005 m^3 Density:1 kg/m^3 Weight:0.000167551 N | C:\Users\fenobus\OneDrive - City, University of London\SolidworksFiles\fs\18650\HB2.SLDPRT Feb 25 17:30:42 2018
Boss-Extrude4 | Solid Body | Mass:2.54546e-006 kg Volume:2.54546e-006 m^3 Density:1 kg/m^3 Weight:2.49455e-005 N | C:\Users\fenobus\OneDrive - City, University of London\SolidworksFiles\fs\18650\EndCap.SLDPRT Feb 26 18:34:28 2018
Boss-Extrude4 | Solid Body | Mass:2.54546e-006 kg Volume:2.54546e-006 m^3 Density:1 kg/m^3 Weight:2.49455e-005 N | C:\Users\fenobus\OneDrive - City, University of London\SolidworksFiles\fs\18650\EndCap.SLDPRT Feb 26 18:34:28 2018
Boss-Extrude3 | Solid Body | Mass:1.70971e-005 kg Volume:1.70971e-005 m^3 Density:1 kg/m^3 Weight:0.000167551 N | C:\Users\fenobus\OneDrive - City, University of London\SolidworksFiles\fs\18650\HB2.SLDPRT Feb 25 17:30:42 2018
Boss-Extrude4 | Solid Body | Mass:2.54546e-006 kg Volume:2.54546e-006 m^3 Density:1 kg/m^3 Weight:2.49455e-005 N | C:\Users\fenobus\OneDrive - City, University of London\SolidworksFiles\fs\18650\EndCap.SLDPRT Feb 26 18:34:28 2018
Boss-Extrude4 | Solid Body | Mass:2.54546e-006 kg Volume:2.54546e-006 m^3 Density:1 kg/m^3 Weight:2.49455e-005 N | C:\Users\fenobus\OneDrive - City, University of London\SolidworksFiles\fs\18650\EndCap.SLDPRT Feb 26 18:34:28 2018
Boss-Extrude3 | Solid Body | Mass:1.70971e-005 kg Volume:1.70971e-005 m^3 Density:1 kg/m^3 Weight:0.000167551 N | C:\Users\fenobus\OneDrive - City, University of London\SolidworksFiles\fs\18650\HB2.SLDPRT Feb 25 17:30:42 2018
Boss-Extrude4 | Solid Body | Mass:2.54546e-006 kg Volume:2.54546e-006 m^3 Density:1 kg/m^3 Weight:2.49455e-005 N | C:\Users\fenobus\OneDrive - City, University of London\SolidworksFiles\fs\18650\EndCap.SLDPRT Feb 26 18:34:28 2018
Boss-Extrude4 | Solid Body | Mass:2.54546e-006 kg Volume:2.54546e-006 m^3 Density:1 kg/m^3 Weight:2.49455e-005 N | C:\Users\fenobus\OneDrive - City, University of London\SolidworksFiles\fs\18650\EndCap.SLDPRT Feb 26 18:34:28 2018
Boss-Extrude3 | Solid Body | Mass:1.70971e-005 kg Volume:1.70971e-005 m^3 Density:1 kg/m^3 Weight:0.000167551 N | C:\Users\fenobus\OneDrive - City, University of London\SolidworksFiles\fs\18650\HB2.SLDPRT Feb 25 17:30:42 2018
Boss-Extrude4 | Solid Body | Mass:2.54546e-006 kg Volume:2.54546e-006 m^3 Density:1 kg/m^3 Weight:2.49455e-005 N | C:\Users\fenobus\OneDrive - City, University of London\SolidworksFiles\fs\18650\EndCap.SLDPRT Feb 26 18:34:28 2018
Boss-Extrude4 | Solid Body | Mass:2.54546e-006 kg Volume:2.54546e-006 m^3 Density:1 kg/m^3 Weight:2.49455e-005 N | C:\Users\fenobus\OneDrive - City, University of London\SolidworksFiles\fs\18650\EndCap.SLDPRT Feb 26 18:34:28 2018
Boss-Extrude3 | Solid Body | Mass:1.70971e-005 kg Volume:1.70971e-005 m^3 Density:1 kg/m^3 Weight:0.000167551 N | C:\Users\fenobus\OneDrive - City, University of London\SolidworksFiles\fs\18650\HB2.SLDPRT Feb 25 17:30:42 2018
Boss-Extrude4 | Solid Body | Mass:2.54546e-006 kg Volume:2.54546e-006 m^3 Density:1 kg/m^3 Weight:2.49455e-005 N | C:\Users\fenobus\OneDrive - City, University of London\SolidworksFiles\fs\18650\EndCap.SLDPRT Feb 26 18:34:28 2018
Boss-Extrude4 | Solid Body | Mass:2.54546e-006 kg Volume:2.54546e-006 m^3 Density:1 kg/m^3 Weight:2.49455e-005 N | C:\Users\fenobus\OneDrive - City, University of London\SolidworksFiles\fs\18650\EndCap.SLDPRT Feb 26 18:34:28 2018
Boss-Extrude3 | Solid Body | Mass:1.70971e-005 kg Volume:1.70971e-005 m^3 Density:1 kg/m^3 Weight:0.000167551 N | C:\Users\fenobus\OneDrive - City, University of London\SolidworksFiles\fs\18650\HB2.SLDPRT Feb 25 17:30:42 2018
Boss-Extrude4 | Solid Body | Mass:2.54546e-006 kg Volume:2.54546e-006 m^3 Density:1 kg/m^3 Weight:2.49455e-005 N | C:\Users\fenobus\OneDrive - City, University of London\SolidworksFiles\fs\18650\EndCap.SLDPRT Feb 26 18:34:28 2018
Boss-Extrude4 | Solid Body | Mass:2.54546e-006 kg Volume:2.54546e-006 m^3 Density:1 kg/m^3 Weight:2.49455e-005 N | C:\Users\fenobus\OneDrive - City, University of London\SolidworksFiles\fs\18650\EndCap.SLDPRT Feb 26 18:34:28 2018
Boss-Extrude3 | Solid Body | Mass:1.70971e-005 kg Volume:1.70971e-005 m^3 Density:1 kg/m^3 Weight:0.000167551 N | C:\Users\fenobus\OneDrive - City, University of London\SolidworksFiles\fs\18650\HB2.SLDPRT Feb 25 17:30:42 2018
Boss-Extrude4 | Solid Body | Mass:2.54546e-006 kg Volume:2.54546e-006 m^3 Density:1 kg/m^3 Weight:2.49455e-005 N | C:\Users\fenobus\OneDrive - City, University of London\SolidworksFiles\fs\18650\EndCap.SLDPRT Feb 26 18:34:28 2018
Boss-Extrude4 | Solid Body | Mass:2.54546e-006 kg Volume:2.54546e-006 m^3 Density:1 kg/m^3 Weight:2.49455e-005 N | C:\Users\fenobus\OneDrive - City, University of London\SolidworksFiles\fs\18650\EndCap.SLDPRT Feb 26 18:34:28 2018
Boss-Extrude3 | Solid Body | Mass:1.70971e-005 kg Volume:1.70971e-005 m^3 Density:1 kg/m^3 Weight:0.000167551 N | C:\Users\fenobus\OneDrive - City, University of London\SolidworksFiles\fs\18650\HB2.SLDPRT Feb 25 17:30:42 2018
Boss-Extrude4 | Solid Body | Mass:2.54546e-006 kg Volume:2.54546e-006 m^3 Density:1 kg/m^3 Weight:2.49455e-005 N | C:\Users\fenobus\OneDrive - City, University of London\SolidworksFiles\fs\18650\EndCap.SLDPRT Feb 26 18:34:28 2018
Boss-Extrude4 | Solid Body | Mass:2.54546e-006 kg Volume:2.54546e-006 m^3 Density:1 kg/m^3 Weight:2.49455e-005 N | C:\Users\fenobus\OneDrive - City, University of London\SolidworksFiles\fs\18650\EndCap.SLDPRT Feb 26 18:34:28 2018
Boss-Extrude3 | Solid Body | Mass:1.70971e-005 kg Volume:1.70971e-005 m^3 Density:1 kg/m^3 Weight:0.000167551 N | C:\Users\fenobus\OneDrive - City, University of London\SolidworksFiles\fs\18650\HB2.SLDPRT Feb 25 17:30:42 2018
Boss-Extrude4 | Solid Body | Mass:2.54546e-006 kg Volume:2.54546e-006 m^3 Density:1 kg/m^3 Weight:2.49455e-005 N | C:\Users\fenobus\OneDrive - City, University of London\SolidworksFiles\fs\18650\EndCap.SLDPRT Feb 26 18:34:28 2018
Boss-Extrude4 | Solid Body | Mass:2.54546e-006 kg Volume:2.54546e-006 m^3 Density:1 kg/m^3 Weight:2.49455e-005 N | C:\Users\fenobus\OneDrive - City, University of London\SolidworksFiles\fs\18650\EndCap.SLDPRT Feb 26 18:34:28 2018
Boss-Extrude3 | Solid Body | Mass:1.70971e-005 kg Volume:1.70971e-005 m^3 Density:1 kg/m^3 Weight:0.000167551 N | C:\Users\fenobus\OneDrive - City, University of London\SolidworksFiles\fs\18650\HB2.SLDPRT Feb 25 17:30:42 2018
Boss-Extrude4 | Solid Body | Mass:2.54546e-006 kg Volume:2.54546e-006 m^3 Density:1 kg/m^3 Weight:2.49455e-005 N | C:\Users\fenobus\OneDrive - City, University of London\SolidworksFiles\fs\18650\EndCap.SLDPRT Feb 26 18:34:28 2018
Boss-Extrude4 | Solid Body | Mass:2.54546e-006 kg Volume:2.54546e-006 m^3 Density:1 kg/m^3 Weight:2.49455e-005 N | C:\Users\fenobus\OneDrive - City, University of London\SolidworksFiles\fs\18650\EndCap.SLDPRT Feb 26 18:34:28 2018
Boss-Extrude3 | Solid Body | Mass:1.70971e-005 kg Volume:1.70971e-005 m^3 Density:1 kg/m^3 Weight:0.000167551 N | C:\Users\fenobus\OneDrive - City, University of London\SolidworksFiles\fs\18650\HB2.SLDPRT Feb 25 17:30:42 2018
Boss-Extrude4 | Solid Body | Mass:2.54546e-006 kg Volume:2.54546e-006 m^3 Density:1 kg/m^3 Weight:2.49455e-005 N | C:\Users\fenobus\OneDrive - City, University of London\SolidworksFiles\fs\18650\EndCap.SLDPRT Feb 26 18:34:28 2018
Boss-Extrude4 | Solid Body | Mass:2.54546e-006 kg Volume:2.54546e-006 m^3 Density:1 kg/m^3 Weight:2.49455e-005 N | C:\Users\fenobus\OneDrive - City, University of London\SolidworksFiles\fs\18650\EndCap.SLDPRT Feb 26 18:34:28 2018
Boss-Extrude3 | Solid Body | Mass:1.70971e-005 kg Volume:1.70971e-005 m^3 Density:1 kg/m^3 Weight:0.000167551 N | C:\Users\fenobus\OneDrive - City, University of London\SolidworksFiles\fs\18650\HB2.SLDPRT Feb 25 17:30:42 2018
Boss-Extrude4 | Solid Body | Mass:2.54546e-006 kg Volume:2.54546e-006 m^3 Density:1 kg/m^3 Weight:2.49455e-005 N | C:\Users\fenobus\OneDrive - City, University of London\SolidworksFiles\fs\18650\EndCap.SLDPRT Feb 26 18:34:28 2018
Boss-Extrude4 | Solid Body | Mass:2.54546e-006 kg Volume:2.54546e-006 m^3 Density:1 kg/m^3 Weight:2.49455e-005 N | C:\Users\fenobus\OneDrive - City, University of London\SolidworksFiles\fs\18650\EndCap.SLDPRT Feb 26 18:34:28 2018
Boss-Extrude3 | Solid Body | Mass:1.70971e-005 kg Volume:1.70971e-005 m^3 Density:1 kg/m^3 Weight:0.000167551 N | C:\Users\fenobus\OneDrive - City, University of London\SolidworksFiles\fs\18650\HB2.SLDPRT Feb 25 17:30:42 2018
Boss-Extrude4 | Solid Body | Mass:2.54546e-006 kg Volume:2.54546e-006 m^3 Density:1 kg/m^3 Weight:2.49455e-005 N | C:\Users\fenobus\OneDrive - City, University of London\SolidworksFiles\fs\18650\EndCap.SLDPRT Feb 26 18:34:28 2018
Boss-Extrude4 | Solid Body | Mass:2.54546e-006 kg Volume:2.54546e-006 m^3 Density:1 kg/m^3 Weight:2.49455e-005 N | C:\Users\fenobus\OneDrive - City, University of London\SolidworksFiles\fs\18650\EndCap.SLDPRT Feb 26 18:34:28 2018
Boss-Extrude3 | Solid Body | Mass:1.70971e-005 kg Volume:1.70971e-005 m^3 Density:1 kg/m^3 Weight:0.000167551 N | C:\Users\fenobus\OneDrive - City, University of London\SolidworksFiles\fs\18650\HB2.SLDPRT Feb 25 17:30:42 2018
Boss-Extrude4 | Solid Body | Mass:2.54546e-006 kg Volume:2.54546e-006 m^3 Density:1 kg/m^3 Weight:2.49455e-005 N | C:\Users\fenobus\OneDrive - City, University of London\SolidworksFiles\fs\18650\EndCap.SLDPRT Feb 26 18:34:28 2018
Boss-Extrude4 | Solid Body | Mass:2.54546e-006 kg Volume:2.54546e-006 m^3 Density:1 kg/m^3 Weight:2.49455e-005 N | C:\Users\fenobus\OneDrive - City, University of London\SolidworksFiles\fs\18650\EndCap.SLDPRT Feb 26 18:34:28 2018
Boss-Extrude3 | Solid Body | Mass:1.70971e-005 kg Volume:1.70971e-005 m^3 Density:1 kg/m^3 Weight:0.000167551 N | C:\Users\fenobus\OneDrive - City, University of London\SolidworksFiles\fs\18650\HB2.SLDPRT Feb 25 17:30:42 2018
Boss-Extrude4 | Solid Body | Mass:2.54546e-006 kg Volume:2.54546e-006 m^3 Density:1 kg/m^3 Weight:2.49455e-005 N | C:\Users\fenobus\OneDrive - City, University of London\SolidworksFiles\fs\18650\EndCap.SLDPRT Feb 26 18:34:28 2018
Boss-Extrude4 | Solid Body | Mass:2.54546e-006 kg Volume:2.54546e-006 m^3 Density:1 kg/m^3 Weight:2.49455e-005 N | C:\Users\fenobus\OneDrive - City, University of London\SolidworksFiles\fs\18650\EndCap.SLDPRT Feb 26 18:34:28 2018
Boss-Extrude3 | Solid Body | Mass:1.70971e-005 kg Volume:1.70971e-005 m^3 Density:1 kg/m^3 Weight:0.000167551 N | C:\Users\fenobus\OneDrive - City, University of London\SolidworksFiles\fs\18650\HB2.SLDPRT Feb 25 17:30:42 2018
Boss-Extrude4 | Solid Body | Mass:2.54546e-006 kg Volume:2.54546e-006 m^3 Density:1 kg/m^3 Weight:2.49455e-005 N | C:\Users\fenobus\OneDrive - City, University of London\SolidworksFiles\fs\18650\EndCap.SLDPRT Feb 26 18:34:28 2018
Boss-Extrude4 | Solid Body | Mass:2.54546e-006 kg Volume:2.54546e-006 m^3 Density:1 kg/m^3 Weight:2.49455e-005 N | C:\Users\fenobus\OneDrive - City, University of London\SolidworksFiles\fs\18650\EndCap.SLDPRT Feb 26 18:34:28 2018
Boss-Extrude3 | Solid Body | Mass:1.70971e-005 kg Volume:1.70971e-005 m^3 Density:1 kg/m^3 Weight:0.000167551 N | C:\Users\fenobus\OneDrive - City, University of London\SolidworksFiles\fs\18650\HB2.SLDPRT Feb 25 17:30:42 2018
Boss-Extrude4 | Solid Body | Mass:2.54546e-006 kg Volume:2.54546e-006 m^3 Density:1 kg/m^3 Weight:2.49455e-005 N | C:\Users\fenobus\OneDrive - City, University of London\SolidworksFiles\fs\18650\EndCap.SLDPRT Feb 26 18:34:28 2018
Boss-Extrude4 | Solid Body | Mass:2.54546e-006 kg Volume:2.54546e-006 m^3 Density:1 kg/m^3 Weight:2.49455e-005 N | C:\Users\fenobus\OneDrive - City, University of London\SolidworksFiles\fs\18650\EndCap.SLDPRT Feb 26 18:34:28 2018
Boss-Extrude3 | Solid Body | Mass:1.70971e-005 kg Volume:1.70971e-005 m^3 Density:1 kg/m^3 Weight:0.000167551 N | C:\Users\fenobus\OneDrive - City, University of London\SolidworksFiles\fs\18650\HB2.SLDPRT Feb 25 17:30:42 2018
Boss-Extrude4 | Solid Body | Mass:2.54546e-006 kg Volume:2.54546e-006 m^3 Density:1 kg/m^3 Weight:2.49455e-005 N | C:\Users\fenobus\OneDrive - City, University of London\SolidworksFiles\fs\18650\EndCap.SLDPRT Feb 26 18:34:28 2018
Boss-Extrude4 | Solid Body | Mass:2.54546e-006 kg Volume:2.54546e-006 m^3 Density:1 kg/m^3 Weight:2.49455e-005 N | C:\Users\fenobus\OneDrive - City, University of London\SolidworksFiles\fs\18650\EndCap.SLDPRT Feb 26 18:34:28 2018
Boss-Extrude3 | Solid Body | Mass:1.70971e-005 kg Volume:1.70971e-005 m^3 Density:1 kg/m^3 Weight:0.000167551 N | C:\Users\fenobus\OneDrive - City, University of London\SolidworksFiles\fs\18650\HB2.SLDPRT Feb 25 17:30:42 2018
Boss-Extrude4 | Solid Body | Mass:2.54546e-006 kg Volume:2.54546e-006 m^3 Density:1 kg/m^3 Weight:2.49455e-005 N | C:\Users\fenobus\OneDrive - City, University of London\SolidworksFiles\fs\18650\EndCap.SLDPRT Feb 26 18:34:28 2018
Boss-Extrude4 | Solid Body | Mass:2.54546e-006 kg Volume:2.54546e-006 m^3 Density:1 kg/m^3 Weight:2.49455e-005 N | C:\Users\fenobus\OneDrive - City, University of London\SolidworksFiles\fs\18650\EndCap.SLDPRT Feb 26 18:34:28 2018
Boss-Extrude3 | Solid Body | Mass:1.70971e-005 kg Volume:1.70971e-005 m^3 Density:1 kg/m^3 Weight:0.000167551 N | C:\Users\fenobus\OneDrive - City, University of London\SolidworksFiles\fs\18650\HB2.SLDPRT Feb 25 17:30:42 2018
Boss-Extrude4 | Solid Body | Mass:2.54546e-006 kg Volume:2.54546e-006 m^3 Density:1 kg/m^3 Weight:2.49455e-005 N | C:\Users\fenobus\OneDrive - City, University of London\SolidworksFiles\fs\18650\EndCap.SLDPRT Feb 26 18:34:28 2018
Boss-Extrude4 | Solid Body | Mass:2.54546e-006 kg Volume:2.54546e-006 m^3 Density:1 kg/m^3 Weight:2.49455e-005 N | C:\Users\fenobus\OneDrive - City, University of London\SolidworksFiles\fs\18650\EndCap.SLDPRT Feb 26 18:34:28 2018
Boss-Extrude3 | Solid Body | Mass:1.70971e-005 kg Volume:1.70971e-005 m^3 Density:1 kg/m^3 Weight:0.000167551 N | C:\Users\fenobus\OneDrive - City, University of London\SolidworksFiles\fs\18650\HB2.SLDPRT Feb 25 17:30:42 2018
Boss-Extrude4 | Solid Body | Mass:2.54546e-006 kg Volume:2.54546e-006 m^3 Density:1 kg/m^3 Weight:2.49455e-005 N | C:\Users\fenobus\OneDrive - City, University of London\SolidworksFiles\fs\18650\EndCap.SLDPRT Feb 26 18:34:28 2018
Boss-Extrude4 | Solid Body | Mass:2.54546e-006 kg Volume:2.54546e-006 m^3 Density:1 kg/m^3 Weight:2.49455e-005 N | C:\Users\fenobus\OneDrive - City, University of London\SolidworksFiles\fs\18650\EndCap.SLDPRT Feb 26 18:34:28 2018
Boss-Extrude3 | Solid Body | Mass:1.70971e-005 kg Volume:1.70971e-005 m^3 Density:1 kg/m^3 Weight:0.000167551 N | C:\Users\fenobus\OneDrive - City, University of London\SolidworksFiles\fs\18650\HB2.SLDPRT Feb 25 17:30:42 2018
Boss-Extrude4 | Solid Body | Mass:2.54546e-006 kg Volume:2.54546e-006 m^3 Density:1 kg/m^3 Weight:2.49455e-005 N | C:\Users\fenobus\OneDrive - City, University of London\SolidworksFiles\fs\18650\EndCap.SLDPRT Feb 26 18:34:28 2018
Boss-Extrude4 | Solid Body | Mass:2.54546e-006 kg Volume:2.54546e-006 m^3 Density:1 kg/m^3 Weight:2.49455e-005 N | C:\Users\fenobus\OneDrive - City, University of London\SolidworksFiles\fs\18650\EndCap.SLDPRT Feb 26 18:34:28 2018
Boss-Extrude3 | Solid Body | Mass:1.70971e-005 kg Volume:1.70971e-005 m^3 Density:1 kg/m^3 Weight:0.000167551 N | C:\Users\fenobus\OneDrive - City, University of London\SolidworksFiles\fs\18650\HB2.SLDPRT Feb 25 17:30:42 2018
Boss-Extrude4 | Solid Body | Mass:2.54546e-006 kg Volume:2.54546e-006 m^3 Density:1 kg/m^3 Weight:2.49455e-005 N | C:\Users\fenobus\OneDrive - City, University of London\SolidworksFiles\fs\18650\EndCap.SLDPRT Feb 26 18:34:28 2018
Boss-Extrude4 | Solid Body | Mass:2.54546e-006 kg Volume:2.54546e-006 m^3 Density:1 kg/m^3 Weight:2.49455e-005 N | C:\Users\fenobus\OneDrive - City, University of London\SolidworksFiles\fs\18650\EndCap.SLDPRT Feb 26 18:34:28 2018
Boss-Extrude3 | Solid Body | Mass:1.70971e-005 kg Volume:1.70971e-005 m^3 Density:1 kg/m^3 Weight:0.000167551 N | C:\Users\fenobus\OneDrive - City, University of London\SolidworksFiles\fs\18650\HB2.SLDPRT Feb 25 17:30:42 2018
Boss-Extrude4 | Solid Body | Mass:2.54546e-006 kg Volume:2.54546e-006 m^3 Density:1 kg/m^3 Weight:2.49455e-005 N | C:\Users\fenobus\OneDrive - City, University of London\SolidworksFiles\fs\18650\EndCap.SLDPRT Feb 26 18:34:28 2018
Boss-Extrude4 | Solid Body | Mass:2.54546e-006 kg Volume:2.54546e-006 m^3 Density:1 kg/m^3 Weight:2.49455e-005 N | C:\Users\fenobus\OneDrive - City, University of London\SolidworksFiles\fs\18650\EndCap.SLDPRT Feb 26 18:34:28 2018
Boss-Extrude3 | Solid Body | Mass:1.70971e-005 kg Volume:1.70971e-005 m^3 Density:1 kg/m^3 Weight:0.000167551 N | C:\Users\fenobus\OneDrive - City, University of London\SolidworksFiles\fs\18650\HB2.SLDPRT Feb 25 17:30:42 2018
Boss-Extrude4 | Solid Body | Mass:2.54546e-006 kg Volume:2.54546e-006 m^3 Density:1 kg/m^3 Weight:2.49455e-005 N | C:\Users\fenobus\OneDrive - City, University of London\SolidworksFiles\fs\18650\EndCap.SLDPRT Feb 26 18:34:28 2018
Boss-Extrude4 | Solid Body | Mass:2.54546e-006 kg Volume:2.54546e-006 m^3 Density:1 kg/m^3 Weight:2.49455e-005 N | C:\Users\fenobus\OneDrive - City, University of London\SolidworksFiles\fs\18650\EndCap.SLDPRT Feb 26 18:34:28 2018
Boss-Extrude3 | Solid Body | Mass:1.70971e-005 kg Volume:1.70971e-005 m^3 Density:1 kg/m^3 Weight:0.000167551 N | C:\Users\fenobus\OneDrive - City, University of London\SolidworksFiles\fs\18650\HB2.SLDPRT Feb 25 17:30:42 2018
Boss-Extrude4 | Solid Body | Mass:2.54546e-006 kg Volume:2.54546e-006 m^3 Density:1 kg/m^3 Weight:2.49455e-005 N | C:\Users\fenobus\OneDrive - City, University of London\SolidworksFiles\fs\18650\EndCap.SLDPRT Feb 26 18:34:28 2018
Boss-Extrude4 | Solid Body | Mass:2.54546e-006 kg Volume:2.54546e-006 m^3 Density:1 kg/m^3 Weight:2.49455e-005 N | C:\Users\fenobus\OneDrive - City, University of London\SolidworksFiles\fs\18650\EndCap.SLDPRT Feb 26 18:34:28 2018
Boss-Extrude3 | Solid Body | Mass:1.70971e-005 kg Volume:1.70971e-005 m^3 Density:1 kg/m^3 Weight:0.000167551 N | C:\Users\fenobus\OneDrive - City, University of London\SolidworksFiles\fs\18650\HB2.SLDPRT Feb 25 17:30:42 2018
Boss-Extrude4 | Solid Body | Mass:2.54546e-006 kg Volume:2.54546e-006 m^3 Density:1 kg/m^3 Weight:2.49455e-005 N | C:\Users\fenobus\OneDrive - City, University of London\SolidworksFiles\fs\18650\EndCap.SLDPRT Feb 26 18:34:28 2018
Boss-Extrude4 | Solid Body | Mass:2.54546e-006 kg Volume:2.54546e-006 m^3 Density:1 kg/m^3 Weight:2.49455e-005 N | C:\Users\fenobus\OneDrive - City, University of London\SolidworksFiles\fs\18650\EndCap.SLDPRT Feb 26 18:34:28 2018
Boss-Extrude3 | Solid Body | Mass:1.70971e-005 kg Volume:1.70971e-005 m^3 Density:1 kg/m^3 Weight:0.000167551 N | C:\Users\fenobus\OneDrive - City, University of London\SolidworksFiles\fs\18650\HB2.SLDPRT Feb 25 17:30:42 2018
Boss-Extrude4 | Solid Body | Mass:2.54546e-006 kg Volume:2.54546e-006 m^3 Density:1 kg/m^3 Weight:2.49455e-005 N | C:\Users\fenobus\OneDrive - City, University of London\SolidworksFiles\fs\18650\EndCap.SLDPRT Feb 26 18:34:28 2018
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

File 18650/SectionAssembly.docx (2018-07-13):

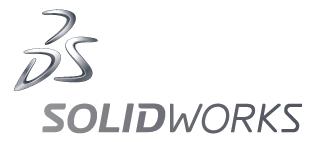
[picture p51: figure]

[company logo here]
[company name here] | [city, state here] | [company url here] | | Sustainability Report

[name] ∙ | [title] | ∙ ∙ [email address] ∙ | (###) ###-####

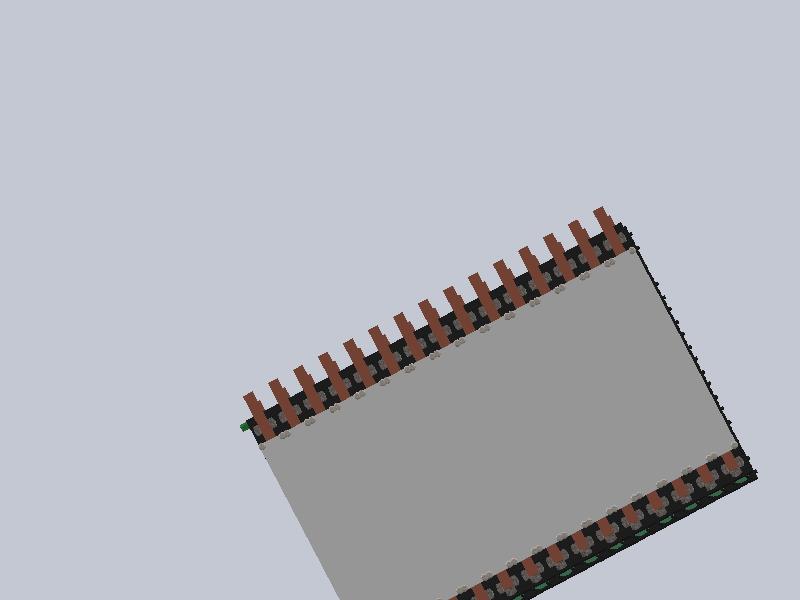
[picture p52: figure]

| | | Model Name: SectionAssembly Weight: 21597.07 g Built to last: 5.0 year Duration of use: 5.0 year


| | | Manufacturing Region The choice of manufacturing region determines the energy sources and technologies used in the modeled material creation and manufacturing steps of the product’s life cycle.
| | | Use Region The use region is used to determine the energy sources consumed during the product’s use phase (if applicable) and the destination for the product at its end-of-life. Together with the manufacturing region, the use region is also used to estimate the environmental impacts associated with transporting the product from its manufacturing location to its use location.

Summary

Learn more about Life Cycle Assessment (http://www.solidworks.com/sustainabilityinfo)

Sustainability Report
Model Name: | | SectionAssembly | | | | | | Weight: | | 21597.07 g
| | | | | | | | Built to last: | | 5.0 year
| | | | | | | | Duration of use: | | 5.0 year
Assembly Process Region: Europe Energy type: None Energy amount: 0.00 kWh Built to last: 5.0 year | | | | | | Use Region: Europe Energy type: None Energy amount: 0.00 kWh Duration of use: 5.0 year
Transportation Truck distance: 1900 km Train distance: 0.00 km Ship distance: 0.00 km Airplane Distance: 0.00 km | | | | | | End of Life Recycled: 33 % Incinerated: 13 % Landfill: 54 %

Comments
Click here for alternative units such as ‘Miles Driven in a Car’ (http://www.solidworks.com/plugins/sustainability/calculator.htm?LANG=en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)

Sustainability Report
Model Name: | | SectionAssembly | | | | | Weight: | | 21597.07 g
| | | | | | | Built to last: | | 5.0 year
| | | | | | | Duration of use: | | 5.0 year

Environmental Impact (calculated using TRACI impact assessment methodology)
Carbon Footprint Material: 280 kg CO2e Manufacturing: 91 kg CO2e Use: 0.00 kg CO2e Transportation: 6.2 kg CO2e End of Life: 12 kg CO2e 390 kg CO2e | | | | | | Total Energy Consumed Material: 3700 MJ Manufacturing: 910 MJ Use: 0.00 MJ Transportation: 82 MJ End of Life: 8.7 MJ 4700 MJ
Air Acidification Material: 57 mol H⁺ e Manufacturing: 61 mol H⁺ e Use: 0.00 mol H⁺ e Transportation: 8.5 mol H⁺ e End of Life: 0.408 mol H⁺ e 130 mol H⁺ e | | | | | | Water Eutrophication Material: 0.359 kg N e Manufacturing: 0.023 kg N e Use: 0.00 kg N e Transportation: 5.2E-3 kg N e End of Life: 3.7E-3 kg N e 0.391 kg N e

Material Financial Impact | 102.70 USD

Comments
Click here for alternative units such as ‘Miles Driven in a Car’ (http://www.solidworks.com/plugins/sustainability/calculator.htm?LANG=en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)

Sustainability Report
Model Name: | | SectionAssembly | | | Weight: | 21597.07 g
| | | | | Built to last: | 5.0 year
| | | | | Duration of use: | 5.0 year

Component Environmental Impact

Top Ten Components Contributing Most to the Four Areas of Environmental Impact

Component | Carbon | | | | | | Water | | | | | | | Air | | | | | | Energy
DummyPCBForSection | 1.3 | | | | | | 3.2E-4 | | | | | | | 0.598 | | | | | | 18
HB2 | 0.520 | | | | | | 5.0E-4 | | | | | | | 0.164 | | | | | | 6.0
DummyPCB | 0.444 | | | | | | 1.1E-4 | | | | | | | 0.199 | | | | | | 6.0
CopperConductor | 0.034 | | | | | | 9.3E-6 | | | | | | | 0.014 | | | | | | 0.439
pan slot head_am | 7.5E-3 | | | | | | 3.7E-5 | | | | | | | 1.4E-3 | | | | | | 0.074
EndCap | 0.016 | | | | | | 5.2E-6 | | | | | | | 5.1E-3 | | | | | | 0.285
EndCapWithM3 | 0.015 | | | | | | 4.8E-6 | | | | | | | 4.8E-3 | | | | | | 0.266

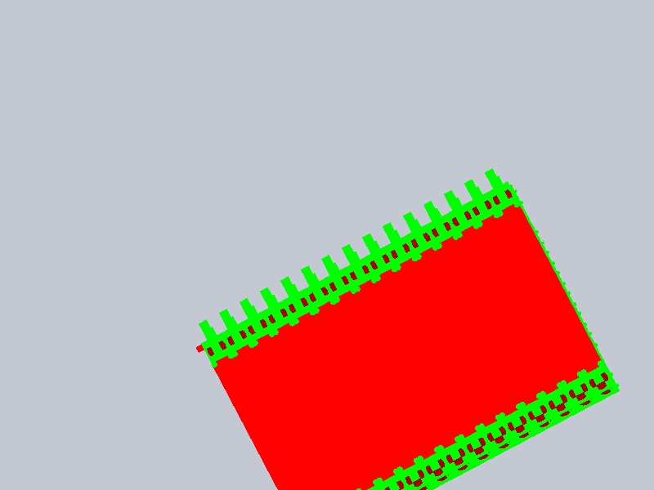
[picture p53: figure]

Comments
Click here for alternative units such as ‘Miles Driven in a Car’ (http://www.solidworks.com/plugins/sustainability/calculator.htm?LANG=en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)

Sustainability Report


Sustainability Report

Glossary

Air Acidification - Sulfur dioxide, nitrous oxides other acidic emissions to air cause an increase in the acidity of rainwater, which in turn acidifies lakes and soil. These acids can make the land and water toxic for plants and aquatic life. Acid rain can also slowly dissolve manmade building materials such as concrete. This impact is typically measured in units of either kg sulfur dioxide equivalent (SO2), or moles H+ equivalent.

Carbon Footprint - Carbon-dioxide and other gasses which result from the burning of fossil fuels accumulate in the atmosphere which in turn increases the earth’s average temperature. Carbon footprint acts as a proxy for the larger impact factor referred to as Global Warming Potential (GWP). Global warming is blamed for problems like loss of glaciers, extinction of species, and more extreme weather, among others.

Total Energy Consumed - A measure of the non-renewable energy sources associated with the part’s lifecycle in units of megajoules (MJ). This impact includes not only the electricity or fuels used during the product’s lifecycle, but also the upstream energy required to obtain and process these fuels, and the embodied energy of materials which would be released if burned. PED is expressed as the net calorific value of energy demand from non-renewable resources (e.g. petroleum, natural gas, etc.). Efficiencies in energy conversion (e.g. power, heat, steam, etc.) are taken into account.

Water Eutrophication - When an over abundance of nutrients are added to a water ecosystem, eutrophication occurs. Nitrogen and phosphorous from waste water and agricultural fertilizers causes an overabundance of algae to bloom, which then depletes the water of oxygen and results in the death of both plant and animal life. This impact is typically measured in either kg phosphate equivalent (PO4) or kg nitrogen (N) equivalent.

Life Cycle Assessment (LCA) - This is a method to quantitatively assess the environmental impact of a product throughout its entire lifecycle, from the procurement of the raw materials, through the production, distribution, use, disposal and recycling of that product.

Material Financial Impact - This is the financial impact associated with the material only. The mass of the model is multiplied by the financial impact unit (units of currency/units of mass) to calculate the financial impact (in units of currency).

Learn more about Life Cycle Assessment (http://www.solidworks.com/sustainabilityinfo)

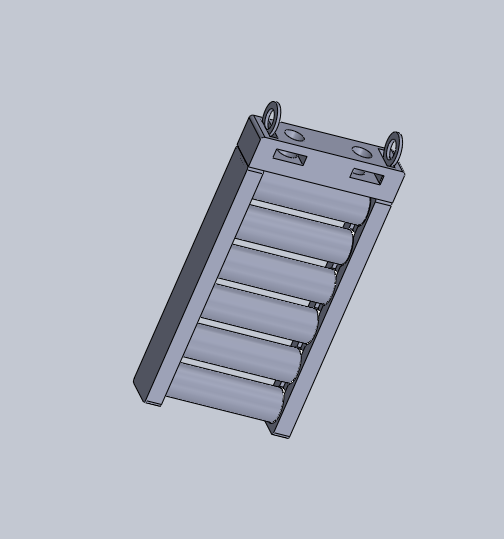
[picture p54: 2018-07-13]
Deliverables/module subassembly.PNG
